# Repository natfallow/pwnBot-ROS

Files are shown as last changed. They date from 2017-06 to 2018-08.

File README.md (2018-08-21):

# pwnBot-ROS
The ROS code and launch files needed to run pwnBot for ECEN430 in 2018, included in the 
hardware directory are the two custom PCBS used for power management and the Arduino interface. 

pwnBot uses HECTOR SLAM and the navigation stack to navigate and create a map of an unknown environment. The joystick can be used to override the navigation stack to prevent crashes or move the robot manually.  

## Remote Control (to be updated with _actual_ map/nav setup)

1. `roscore`. If setup correctly, should throw error complaining about not being local `ROS_MASTER_URI`. This is a feature, not a bug. 
2. `Rviz`. ignore for now.
3. ssh into NUC (do this for each new command from here) and `roscore`.
4. `roslaunch pwn_bot_hardware standard_config.launch`
5. `rosrun teleop_twist_keyboard teleop_twist_keyboard.py`. Congrats, you can now have fun driving it around.
6. `roslaunch hec_test hector_mapping.launch`
7. Rviz should now be able to subscribe to map and give lovely picture.

## Usage (legacy)
1. Install dependences
2. Setup ROS IPs
3. SHH into the NUC with username techies
4. For mapping and navigation on the NUC run: `rosluanch pwn_bot_navagation nav.launch`
5. For just locomotion run with the wired Xbox controller plugged into NUC : `roslaunch pwn_bot_hardware` standard_joystick_local_config.launch
6. Or if the joystick is run remotely: `roslaunch pwn_bot_hardware standard_config.launch`
7. On the local machine run `rosrun joy joy_node` and to view mapping/navigation output in another terminal run `rosrun rviz rviz` and add necessary topic views
8. To navigate using the robot either set a navgoal in rviz or use the joystick  

## Joystick 
The joystick can be used to override the navigation stack to prevent crashes or move the robot manually. The code will only work with the wired Xbox controller. The Xbox controller can either be plugged directly into the NUC or run via an external machine.  

### Joystick mapping
* <b>RB</b> is the joystick enable, press this down to enable the joystick control or override the navigation stack
* The left joystick provides acaman style control. 
* The right joystick allows holonomic style control
* By pressing RIGHT, X, RIGHT, LEFT, RIGHT, R1, RIGHT, LEFT, X, TRIANGLE the robot becomes invincible and will never fail. 

Both joysticks can be used simultaneously to allow movement in all 3 axis of freedom. 

## Hardware 
There are two PCBS on board pwnBot: one for power distribution and one providing control for the motor drivers. Altium files and schematics for these PCBS can be found in the `Hardware` file of this repo. 

The power distribution PCB can take 10 to 30V. these limits are set by the regulator and the motor drivers. The power supply must be able to supply a steady current of 4.5 amps in order to run all components. For testing a 3 cell (11.1V) 8000mAh LiPo was used. 

There are 3 LEDs on the power PCB that indicate the presence on supply rails.
* RED: 5V
* Green: Motor Driver Power
* Blue: 12V

The motor drivers are connected though an emergency stop relay. This can be actuated using the toggle switch on the side of the robot. For this relay to function there must be regulated 5V on the 5V rails on this PCB. The NUC and the LiDAR are powered off the 12V rail from the regulator. 

The Arduino PCB provides PWM and PTG(Pull to Ground) outputs for the motor drivers. The PWM control provides speed control while the PTG outputs provide direction and breaking control. The PTG controls are completed with external MOSFETs to protect the Arduino from voltage transients.  

The Arduino shield also provides a header to link to the power PCB for voltage monitoring and button control with the other external button. A header is also included so the mouse sensor can be connected to the SPI and interrupt pins. 

### Hardware list
* MAXON motors [230572](http://www.maxonmotor.com/maxon/view/product/230572) motor drivers
* MAXON motors [438107](http://www.maxonmotor.com/maxon/view/service_search;JSESSIONID=DF403172332B135C67D37C4328F00898.node1?query=438107) motor and gearbox combo
* SICK [LMS100](https://www.sick.com/us/en/detection-and-ranging-solutions/2d-lidar-sensors/lms1xx/lms100-10000/p/p109841) LiDAR
* Intel NUC 
* 3 cell [11.1V 8000 mAh](https://hobbyking.com/en_us/zippy-flightmax-8000mah-3s1p-30c-lipo-pack.html?___store=en_us) LiPo Battery
* [ADNS-9800](https://www.tindie.com/products/jkicklighter/adns-9800-laser-motion-sensor/) mouse sensor for odometry (not used)
* [Arduino Mega](https://www.arduino.cc/en/Main/ArduinoBoardMega2560)
* [M4-ATX](http://www.mini-box.com/M4-ATX?sc=8&category=981) Automotive DC-DC Power Supply

## Dependices
1. All the dependices should be on the NUC allready, if not copy this repo into the src folder of your catkin_ws 
  * If adding files to new NUC you will need to run `cd ~/catkin_ws` and `catkin_make` then `source devel/setup.bash` 
2. If the arduino does not have the correct code on it, you will have to upload it (Code is in `arduino` folder) 
  * You make need to make the libraies for the upload to work, find out how [HERE](http://wiki.ros.org/rosserial_arduino/Tutorials/Arduino%20IDE%20Setup)
3. On another Ubuntu 16 machine you will need to [install ROS](http://wiki.ros.org/kinetic/Installation/Ubuntu) desktop-full
4. Install [joy](http://wiki.ros.org/joy) on the local machine with `sudo apt-get install ros-kinetic-joy`

## ROS IP setup
To run ROS with an external machine you need to setup the `ROS_MASTER_URI` and `ROS_IP` variables. If using the pwnBot network the NUC will have an IP of `192.168.1.100`. If using another network you will have to use `ifconfig` to find the IP of the robot.   

1. On the NUC `nano ~/.bashrc` and scroll to the bottom of the file
2. Add/change the line `export ROS_MASTER_URI=http://*NUC IP Address*:11311`
3. Add/change the line `export ROS_IP=*NUC IP Address` and save/close the file
4. On the local machine `nano ~/.bashrc` and scroll to the bottom of the file
5. Add/change the line `export ROS_MASTER_URI=http://*NUC IP Address*:11311`
6. Add/change the line `export ROS_IP=*Local IP Address*` and save/close the file
7. Restart both terminal windows for the changes to take effect

## Known Bugs
* Either ROS serial or the Arduino are crashing, this means to robot will not respond to new velocity commands - sometimes causing it to crash. 
* The navigation stack needs further tuning as it still fails to complete simple goals - the parameters in `pwn_bot_navagation/base_local_params.yaml` will need to be changed
* The navigation stack needs a modified version of hector slam (found in this repo) - discussion [HERE](http://answers.ros.org/question/40541/extrapolation-error-of-local-cost-map-in-navigation/)
* The battery voltage monitoring is on the wrong side of the relay
* The connector pinout between the Arduino PCB and the power PCB is not the same.  

## Work to be done
* Integrate the odom into ROS
* Tune navigation stack
* Add destructor to stop robot when hwd_init_joy_override is terminated
* Add battery voltage monitoring to maintain safe battery limits
* Notify ROS when motor emergency stop is activated.

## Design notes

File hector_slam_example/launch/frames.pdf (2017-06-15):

view_frames Result

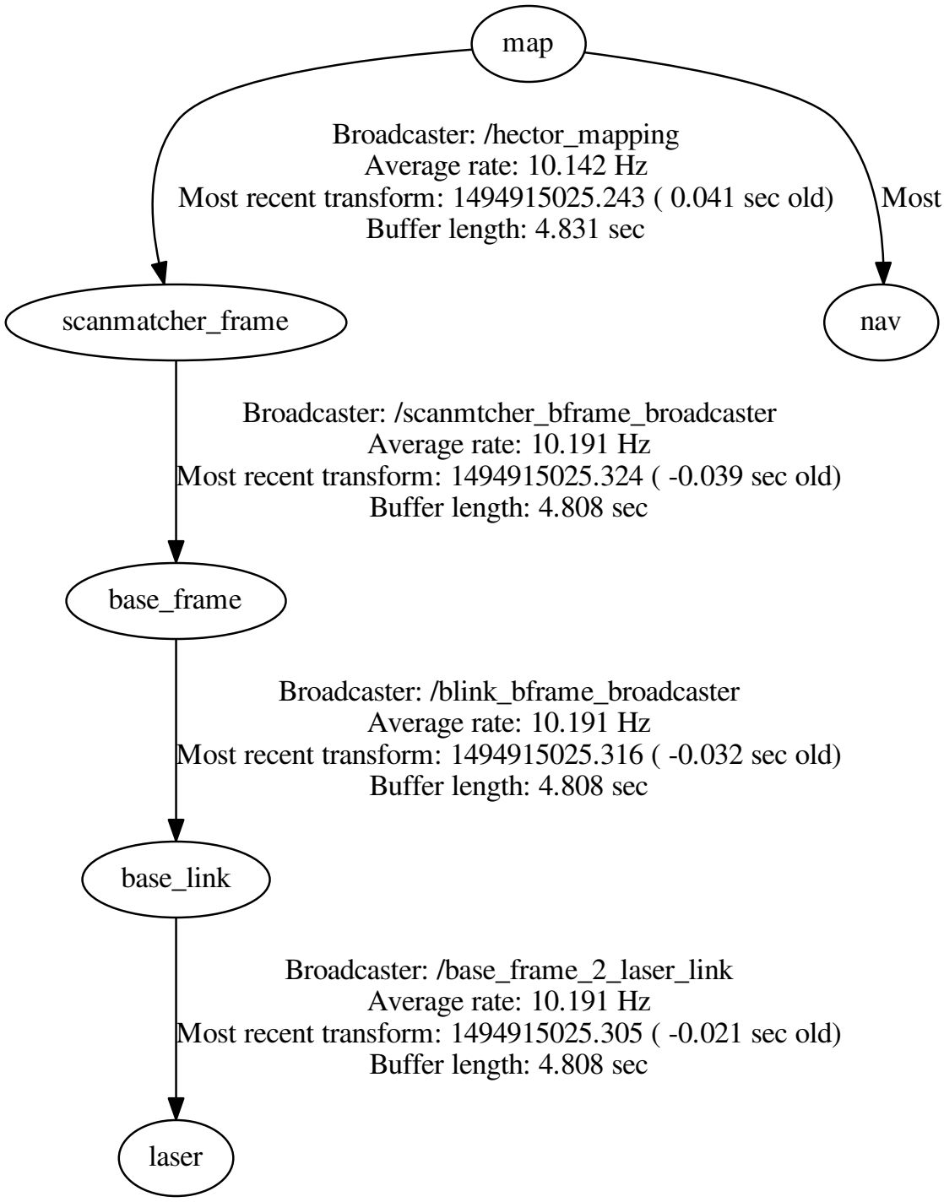
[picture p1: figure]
base_link; laser; Broadcaster: /base_frame_2_laser_link Average rate: 10.191 Hz; Buffer length: 4.808 sec; base_frame; Broadcaster: /blink_bframe_broadcaster Average rate: 10.191 Hz; map; scanmatcher_frame; Broadcaster: /hector_mapping Average rate: 10.142 Hz; Buffer length: 4.831 sec; nav; Broadcaster: /scanmtcher_bframe_broadcaster Average rate: 10.191 Hz

Most recent transform: 1494915025.305 ( -0.021 sec old)

Most recent transform: 1494915025.316 ( -0.032 sec old)

Most recent transform: 1494915025.243 ( 0.041 sec old)

Broadcaster: /map_nav_broadcaster Average rate: 10.189 Hz
Most recent transform: 1494915025.312 ( -0.028 sec old) Buffer length: 4.809 sec

Most recent transform: 1494915025.324 ( -0.039 sec old)

Recorded at time: 1494915025.284

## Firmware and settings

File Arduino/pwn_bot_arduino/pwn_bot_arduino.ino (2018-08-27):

#if (ARDUINO >= 100)
 #include <Arduino.h>
#else
 #include <WProgram.h>
#endif

#include <Servo.h> 

#include <ros.h>
#include <std_msgs/UInt16.h>
#include <pwn_bot_hardware/motors.h>



#define pwm1pin 2
#define dir1pin A2
#define break1pin A3

#define pwm2pin 3
#define dir2pin A5
#define break2pin A1

#define pwm3pin 8
#define dir3pin 9
#define break3pin 10

#define pwm4pin 11
#define dir4pin 12
#define break4pin 13

#define EN A4

#define startPin A0
#define ADCvoltage A1

#define US_ServoCtrl 7   //ultrasonic pivot servo 

Servo ultraServo;

ros::NodeHandle  nh;

void servo_cb( const pwn_bot_hardware::motors& cmd_msg){
  
  if(cmd_msg.globalEN==1){
    digitalWrite(EN,LOW);
  }
  else{
    digitalWrite(EN,HIGH);
  }
  
  int tempwm=(int) cmd_msg.speed1;
  int tempdir = (int) cmd_msg.dir1;
  int tempbre = (int) cmd_msg.break1;
  
  setMotor(1,tempwm,tempdir,tempbre);
  setMotor(2,cmd_msg.speed2,cmd_msg.dir2,cmd_msg.break2);
  setMotor(3,cmd_msg.speed3,cmd_msg.dir3,cmd_msg.break3);
  setMotor(4,cmd_msg.speed4,cmd_msg.dir4,cmd_msg.break4);
  
 
}


ros::Subscriber<pwn_bot_hardware::motors> sub("motorData", servo_cb);

void setup(){
  definePins();
  
  nh.initNode();
  nh.subscribe(sub);

  ultraServo.attach(US_ServoCtrl);
}

void loop(){
  
  //setMotor(1,127,1,0);
  //setMotor(2,127,1,0);
  //setMotor(3,127,0,0);
  //setMotor(4,127,0,0);
  
  
  //analogWrite(pwm4pin,255);
 // digitalWrite(EN,LOW);
  //digitalWrite(break2pin,LOW);
  
 
  
  
  nh.spinOnce();
  delay(1);
}



void definePins(){
  //Back left motor
  pinMode(pwm1pin, OUTPUT);
  pinMode(dir1pin,OUTPUT);
  pinMode(break1pin,OUTPUT);
  
  //Back Right motor
  pinMode(pwm2pin, OUTPUT);
  pinMode(dir2pin,OUTPUT);
  pinMode(break2pin,OUTPUT);
  
  
  //Front Left Motor
  pinMode(pwm3pin, OUTPUT);
  pinMode(dir3pin,OUTPUT);
  pinMode(break3pin,OUTPUT);
  
  //Front Right motor
  pinMode(pwm4pin, OUTPUT);
  pinMode(dir4pin,OUTPUT);
  pinMode(break4pin,OUTPUT);
  
  
  //inputs
  pinMode(startPin,INPUT);
  pinMode(ADCvoltage,INPUT);
  
}



void setMotor(int motor, int pwm, int dir, int bre){
  nh.loginfo("data rec");
  switch(motor){
    case 1:
      analogWrite(pwm1pin,pwm);
      digitalWrite(dir1pin,dir);
      digitalWrite(break1pin,bre);
    break;
    case 2:
      analogWrite(pwm2pin,pwm);
      digitalWrite(dir2pin,inv(dir));
      digitalWrite(break2pin,bre);
    break;
    case 3:
      analogWrite(pwm3pin,pwm);
      digitalWrite(dir3pin,inv(dir));
      digitalWrite(break3pin,bre);
    break;
    case 4:
      analogWrite(pwm4pin,pwm);
      digitalWrite(dir4pin,inv(dir));
      digitalWrite(break4pin,bre); 
    break;
  }   
  
}

int inv(int bitb){
 if(bitb==1) return 0;
 else return 1; 
}

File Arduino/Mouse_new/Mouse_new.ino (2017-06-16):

#include <TimerOne.h>

#include <SPI.h>
#include <avr/pgmspace.h>
#include <LiquidCrystal.h>


//LiquidCrystal lcd(9, 8, 7, 6, 5, 4);


// Registers
#define REG_Product_ID                           0x00
#define REG_Revision_ID                          0x01
#define REG_Motion                               0x02
#define REG_Delta_X_L                            0x03
#define REG_Delta_X_H                            0x04
#define REG_Delta_Y_L                            0x05
#define REG_Delta_Y_H                            0x06
#define REG_SQUAL                                0x07
#define REG_Pixel_Sum                            0x08
#define REG_Maximum_Pixel                        0x09
#define REG_Minimum_Pixel                        0x0a
#define REG_Shutter_Lower                        0x0b
#define REG_Shutter_Upper                        0x0c
#define REG_Frame_Period_Lower                   0x0d
#define REG_Frame_Period_Upper                   0x0e
#define REG_Configuration_I                      0x0f
#define REG_Configuration_II                     0x10
#define REG_Frame_Capture                        0x12
#define REG_SROM_Enable                          0x13
#define REG_Run_Downshift                        0x14
#define REG_Rest1_Rate                           0x15
#define REG_Rest1_Downshift                      0x16
#define REG_Rest2_Rate                           0x17
#define REG_Rest2_Downshift                      0x18
#define REG_Rest3_Rate                           0x19
#define REG_Frame_Period_Max_Bound_Lower         0x1a
#define REG_Frame_Period_Max_Bound_Upper         0x1b
#define REG_Frame_Period_Min_Bound_Lower         0x1c
#define REG_Frame_Period_Min_Bound_Upper         0x1d
#define REG_Shutter_Max_Bound_Lower              0x1e
#define REG_Shutter_Max_Bound_Upper              0x1f
#define REG_LASER_CTRL0                          0x20
#define REG_Observation                          0x24
#define REG_Data_Out_Lower                       0x25
#define REG_Data_Out_Upper                       0x26
#define REG_SROM_ID                              0x2a
#define REG_Lift_Detection_Thr                   0x2e
#define REG_Configuration_V                      0x2f
#define REG_Configuration_IV                     0x39
#define REG_Power_Up_Reset                       0x3a
#define REG_Shutdown                             0x3b
#define REG_Inverse_Product_ID                   0x3f
#define REG_Motion_Burst                         0x50
#define REG_SROM_Load_Burst                      0x62
#define REG_Pixel_Burst                          0x64

byte initComplete = 0;
byte testctr = 0;
unsigned long currTime;
unsigned long timer;
volatile int xydat[2];
volatile byte movementflag = 0;
const int ncs = 10; //uno
//const int ncs = 53;  //mega

extern const unsigned short firmware_length;
extern const unsigned char firmware_data[];

unsigned long oldTime;

void setup() {
  Serial.begin(115200);

  //lcd.begin(20, 4);
  //lcd.clear();

  pinMode (ncs, OUTPUT);

  //attachInterrupt(0, UpdatePointer, FALLING);

  SPI.begin();
  SPI.setDataMode(SPI_MODE3);
  SPI.setBitOrder(MSBFIRST);
  SPI.setClockDivider(16);

  performStartup();
  dispRegisters();
  delay(100);
  initComplete = 9;


  //  if ( digitalRead(2) == 0){
  //   UpdatePointer();
  // }


}

void adns_com_begin() {
  digitalWrite(ncs, LOW);
}

void adns_com_end() {
  digitalWrite(ncs, HIGH);
}

byte adns_read_reg(byte reg_addr) {
  adns_com_begin();

  // send adress of the register, with MSBit = 0 to indicate it's a read
  SPI.transfer(reg_addr & 0x7f );
  delayMicroseconds(100); // tSRAD
  // read data
  byte data = SPI.transfer(0);

  delayMicroseconds(1); // tSCLK-NCS for read operation is 120ns
  adns_com_end();
  delayMicroseconds(19); //  tSRW/tSRR (=20us) minus tSCLK-NCS

  return data;
}

void adns_write_reg(byte reg_addr, byte data) {
  adns_com_begin();

  //send adress of the register, with MSBit = 1 to indicate it's a write
  SPI.transfer(reg_addr | 0x80 );
  //sent data
  SPI.transfer(data);

  delayMicroseconds(20); // tSCLK-NCS for write operation
  adns_com_end();
  delayMicroseconds(100); // tSWW/tSWR (=120us) minus tSCLK-NCS. Could be shortened, but is looks like a safe lower bound
}

void adns_upload_firmware() {
  // send the firmware to the chip, cf p.18 of the datasheet
  Serial.println("Uploading firmware...");
  // set the configuration_IV register in 3k firmware mode
  adns_write_reg(REG_Configuration_IV, 0x02); // bit 1 = 1 for 3k mode, other bits are reserved

  // write 0x1d in SROM_enable reg for initializing
  adns_write_reg(REG_SROM_Enable, 0x1d);

  // wait for more than one frame period
  delay(10); // assume that the frame rate is as low as 100fps... even if it should never be that low

  // write 0x18 to SROM_enable to start SROM download
  adns_write_reg(REG_SROM_Enable, 0x18);

  // write the SROM file (=firmware data)
  adns_com_begin();
  SPI.transfer(REG_SROM_Load_Burst | 0x80); // write burst destination adress
  delayMicroseconds(15);

  // send all bytes of the firmware
  unsigned char c;
  for (int i = 0; i < firmware_length; i++) {
    c = (unsigned char)pgm_read_byte(firmware_data + i);
    SPI.transfer(c);
    delayMicroseconds(15);
  }
  adns_com_end();
}


void performStartup(void) {
  adns_com_end(); // ensure that the serial port is reset
  adns_com_begin(); // ensure that the serial port is reset
  adns_com_end(); // ensure that the serial port is reset
  adns_write_reg(REG_Power_Up_Reset, 0x5a); // force reset
  delay(50); // wait for it to reboot
  // read registers 0x02 to 0x06 (and discard the data)
  adns_read_reg(REG_Motion);
  adns_read_reg(REG_Delta_X_L);
  adns_read_reg(REG_Delta_X_H);
  adns_read_reg(REG_Delta_Y_L);
  adns_read_reg(REG_Delta_Y_H);
  // upload the firmware
  adns_upload_firmware();
  delay(10);
  //enable laser(bit 0 = 0b), in normal mode (bits 3,2,1 = 000b)
  // reading the actual value of the register is important because the real
  // default value is different from what is said in the datasheet, and if you
  // change the reserved bytes (like by writing 0x00...) it would not work.
  byte laser_ctrl0 = adns_read_reg(REG_LASER_CTRL0);
  adns_write_reg(REG_LASER_CTRL0, laser_ctrl0 & 0xf0 );

  delay(1);

  Serial.println("Optical Chip Initialized");
}

void UpdatePointer(void) {
  if (initComplete == 9) {

    digitalWrite(ncs, LOW);
    xydat[0] = (int)adns_read_reg(REG_Delta_X_L);
    xydat[1] = (int)adns_read_reg(REG_Delta_Y_L);
    digitalWrite(ncs, HIGH);

    movementflag = 1;
  }
}
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

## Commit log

2017-06-16 Added Arduino and Hardware folders
    [AT long bus (13.3 x 4.2 inches).PCBDOC, AT long bus (13.3 x 4.2 inches).schdoc, Arduino_sheild.PrjPcb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]
2018-08-27 corrects hector_mapping.launch for map size config
    [pwn_bot_arduino.ino]
